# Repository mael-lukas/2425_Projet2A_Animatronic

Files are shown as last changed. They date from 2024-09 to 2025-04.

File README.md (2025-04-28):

<h1 align="center"> DEA : Dynamic Eagle Animatronic</h1>

<p align="center">An english version of this README file can be found below the french one</p>

<h2 align="center">Préambule</h2>
Depuis la Grêce antique et le mythe du géant de bronze Talos, les hommes ont toujours cherchés à créer des automates avec les moyens à leur disposition. Les animatroniques sont l'achèvement actuel de ce désir. Ce sont des poupées mécaniques plus ou moins réalistes dont le fonctionnement interne fait intervenir autant la mécanique que l'électronique.
Elles sont, depuis plusieurs décennies, et encore aujourd'hui principalement utilisées dans le domaine du divertissement au travers des parcs d'attractions, des films et des séries.

Dans le cadre d'un projet de deuxième année à l'école d'ingénieur française ENSEA ( École Nationale Supérieure de l'Électronique et de ses Applications), nous allons continuer la création d'une animatronique d'aigle royal démarrée au second semestre de l'année dernière.

# Sommaire 
  * #### Équipe et détail des tâches
  * #### Électronique et CAO
  * #### Modélisation & Impression 3D
  * #### Mécanique
  * #### Informatique
  * #### Résultat final
  * #### Points d'amélioration
  * #### Conclusion

<table>
  <tr>
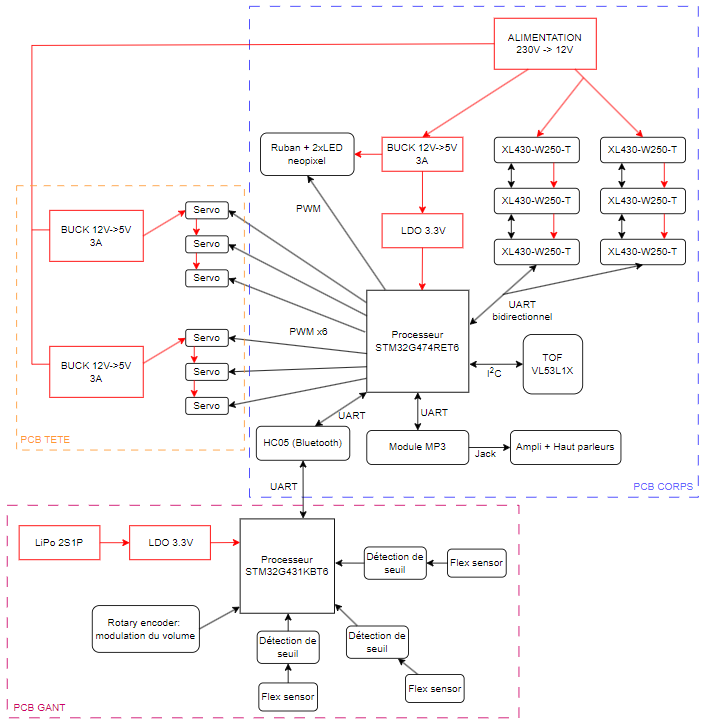
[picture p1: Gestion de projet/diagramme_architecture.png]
Diagramme d'architecture
    <td></td>
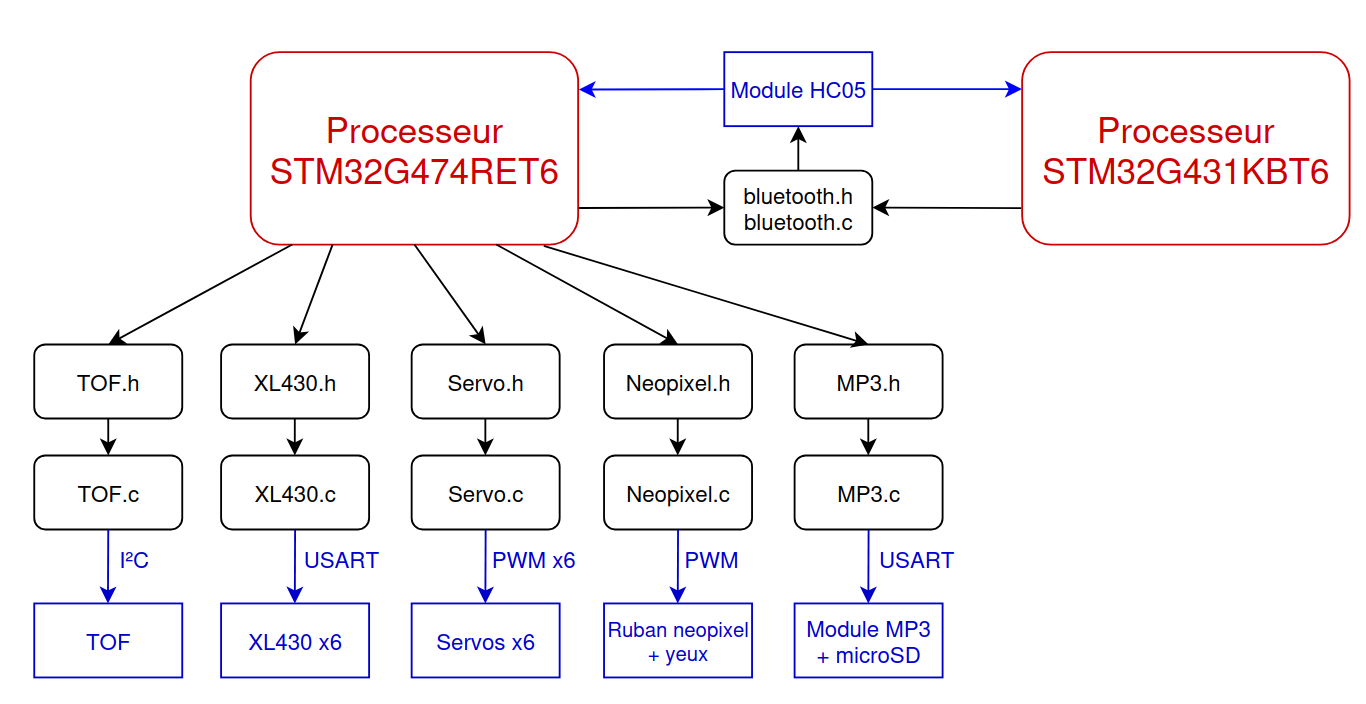
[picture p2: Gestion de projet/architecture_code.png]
Diagramme d'architecture du code
    <td></td>
  </tr>
</table>

<h1 align="center">Équipe</h1>

Membres de l'équipe : 
* #### Vincent Fernandes
    * [Github](https://github.com/FernandesVincent)
    * [Linkedin](https://www.linkedin.com/in/vincent-fernandes-0981552a6/)
* #### Maël Lukas
    * [Github](https://github.com/mael-lukas)
    * [Linkedin](https://www.linkedin.com/in/mael-lukas/)
* ##### Romane Ponthieu
    * [Github](https://github.com/Romanepnth)
    * [Linkedin](https://www.linkedin.com/in/romane-ponthieu/)
* #### Sedrenn Labrousse
    * [Github](https://github.com/Sedrennl)
    * [Linkedin](https://www.linkedin.com/in/sédrenn-labrousse-24b2a5295/)

* #### Supervisé par Nicolas Papazoglou
    * [Github](https://github.com/DBXYD?tab=overview&from=2024-05-01&to=2024-05-29)
    * [Linkedin](https://www.linkedin.com/in/nicolas-papazoglou-38382646/?originalSubdomain=fr)
 
* #### Supervisé par Laurent Fiack
    * [Github](https://github.com/lfiack)
    * [Linkedin](https://fr.linkedin.com/in/laurent-fiack-1b1415124)

Nous vous invitons à consulter notre [github de l'année dernière](https://github.com/mael-lukas/2324_Projet1AB_Animatronic), dans lequel vous pourrez trouver toutes les bases sur lesquelles nous avons démarré ce projet.

Ce projet s'articule autour de plusieurs compétences techniques : informatique, électronique & CAO, modélisation & impression 3D et mécanique. Chacune ayant partagée entre différents membres de l'équipe.

   * Informatique

Cette partie a été majoritairement traitée par Maël avec également, de manière plus minoritaire, Vincent.
Dans cette partie nous allons voir comment tout le code nécessaire au bon fonctionnement du DEA se présente. En partant de simple envoies de PWM pour commander des servomoteurs à la programmation de moteurs plus complexes, en passant par l'allumage de LED neopxiel et de la communication Bluetooth.

   * Électronique & CAO

Cette partie concerne différentes sous compétences : la conception des PCB, la soudure de ceux-ci, les test associés et finalement le sertissage et cablâge. 
Comme notre projet inclus plusieurs PCBs, leur conception a été réalisée par Vincent (pour les PCBs du corps et du gant) et Romane (pour le PCB de la tête).
Les soudures CMS ont été réalisées par Maël et Romane, tandis que les soudures THT ont été effectuées par Vincent.
Le sertissage et le cablâge ont également été réalisé par Vincent.

   * Modélisation & Impression 3D

Cette partie a été essentiellement traitée par Sedrenn aidée de Romane et Vincent. L'objectif de celle-ci étant de modéliser et d'imprimer l'aigle en taille 1:1 ainsi que des caches pour protéger l'alimentation et les PCBs.

   * Mécanique

Cette partie concerne la gestion des différents moteurs qui a été faite par Maël pour l'implémentation du code, par Vincent pour le cablâge de ceux-ci et leur placement sur la structure de l'aigle mais également par Sedrenn et Romane pour la conception des pièces 3D permettant de faire les liaisons entre ceux-ci.

<h1 align="center">Électronique & CAO</h1>

Pour commencer, veuillez trouver ci-dessous le diagramme d'architecture qui nous a servis de base pour la création des PCB de ce projet:

<div align="center">
  Diagramme d'architecture
</div>

Voici donc, le schematic et le routage du PCB principal de projet, le PCB du corps :

<table>
  <tr>
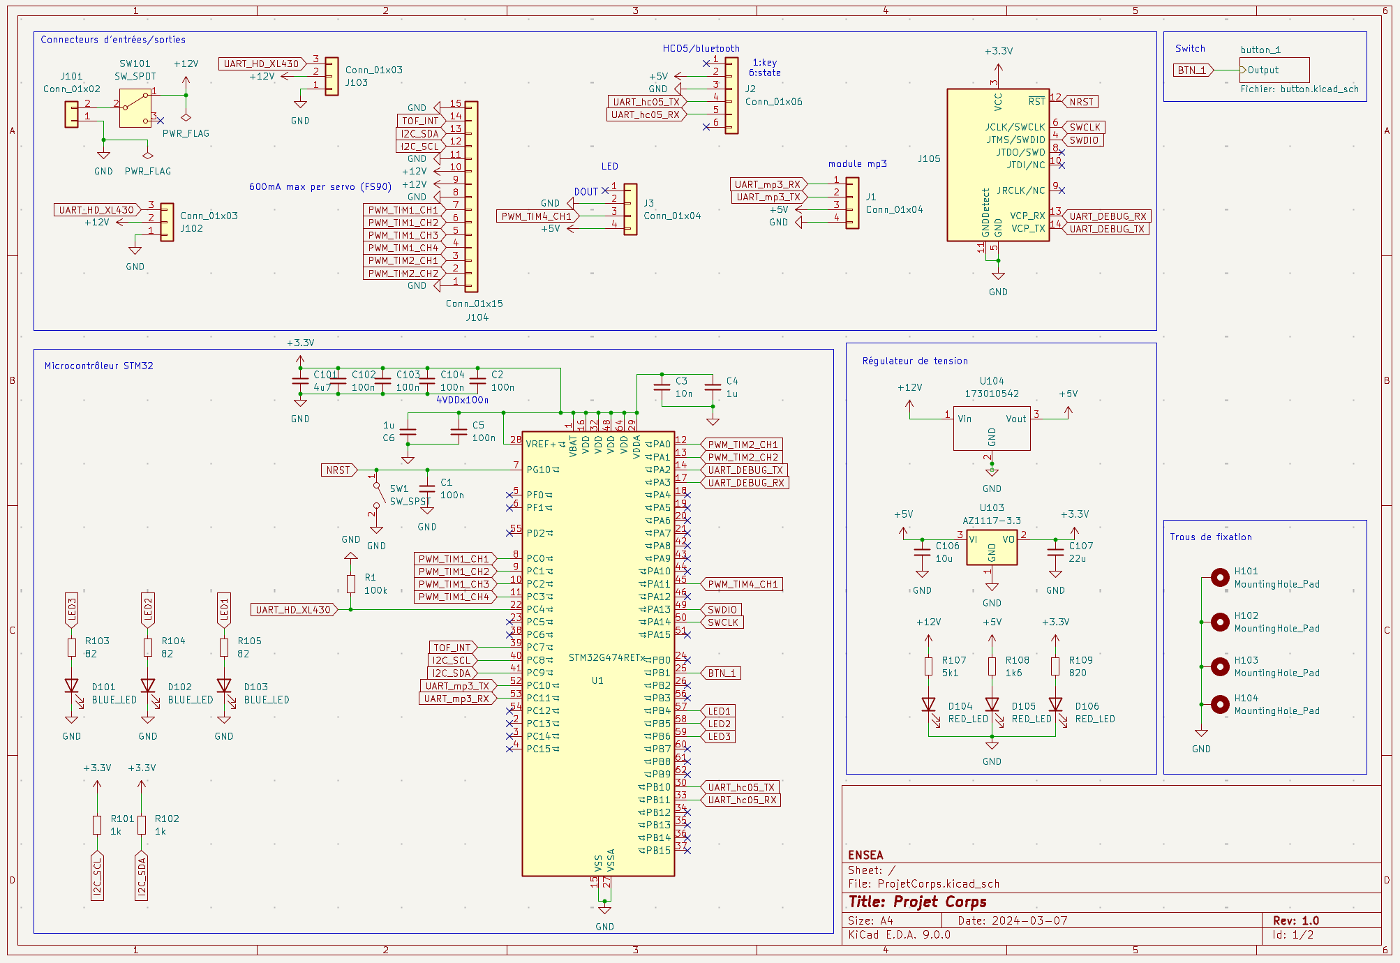
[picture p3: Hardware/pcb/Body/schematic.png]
Schematic
    <td></td>
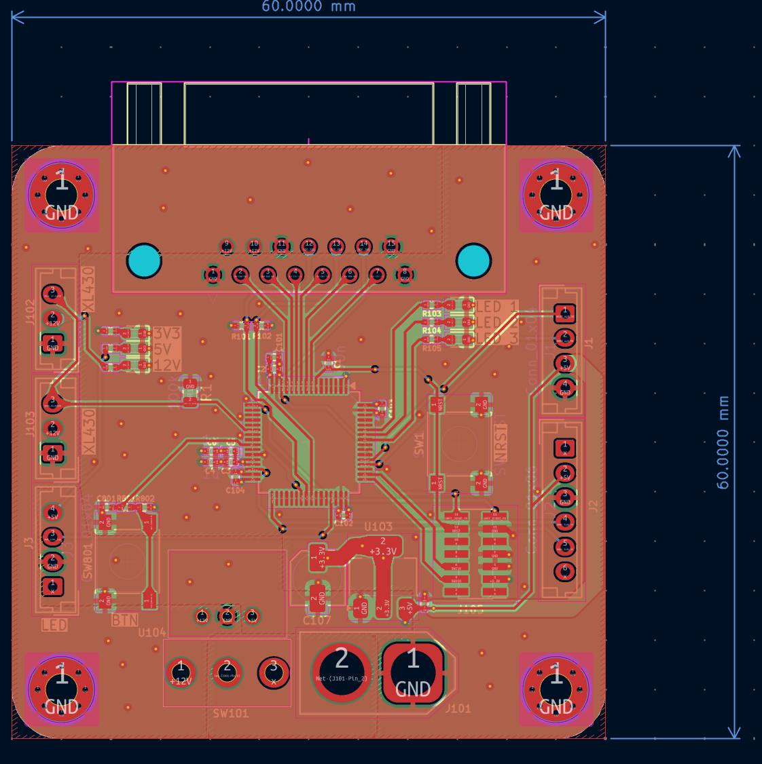
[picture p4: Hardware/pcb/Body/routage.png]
Routage
    <td></td>
  </tr>
</table>

Ce PCB a eu le droit à plusieurs versions afin de l'améliorer à chaque ittération. La dernière en date est l'ajout de R1, une résistance de pull-up pour le protocol UART qui nous sert à commander les moteurs. Cependant, une fois ce nouveau PCB soudé et testé nous n'arrivions plus à communiquer avec les moteurs donc nous sommes repassé sur la version antérieure du PCB, qui elle est foncitonnel, où la résistance de pull-up est activée sur STM32CubeIDE.
Vous pouvez trouvez [ici](https://github.com/mael-lukas/2425_Projet2A_Animatronic/blob/main/Hardware/pcb/Body/ProjetCorps.csv)la BOM de ce PCB.

Le second PCB que nous avons du réalisé est celui de la tête, vous constaterez qu'il n'a pas changé depuis [l'année dernière](https://github.com/mael-lukas/2324_Projet1AB_Animatronic) voici donc simplement son schematic, son routage et sa BOM :

<table>
  <tr>
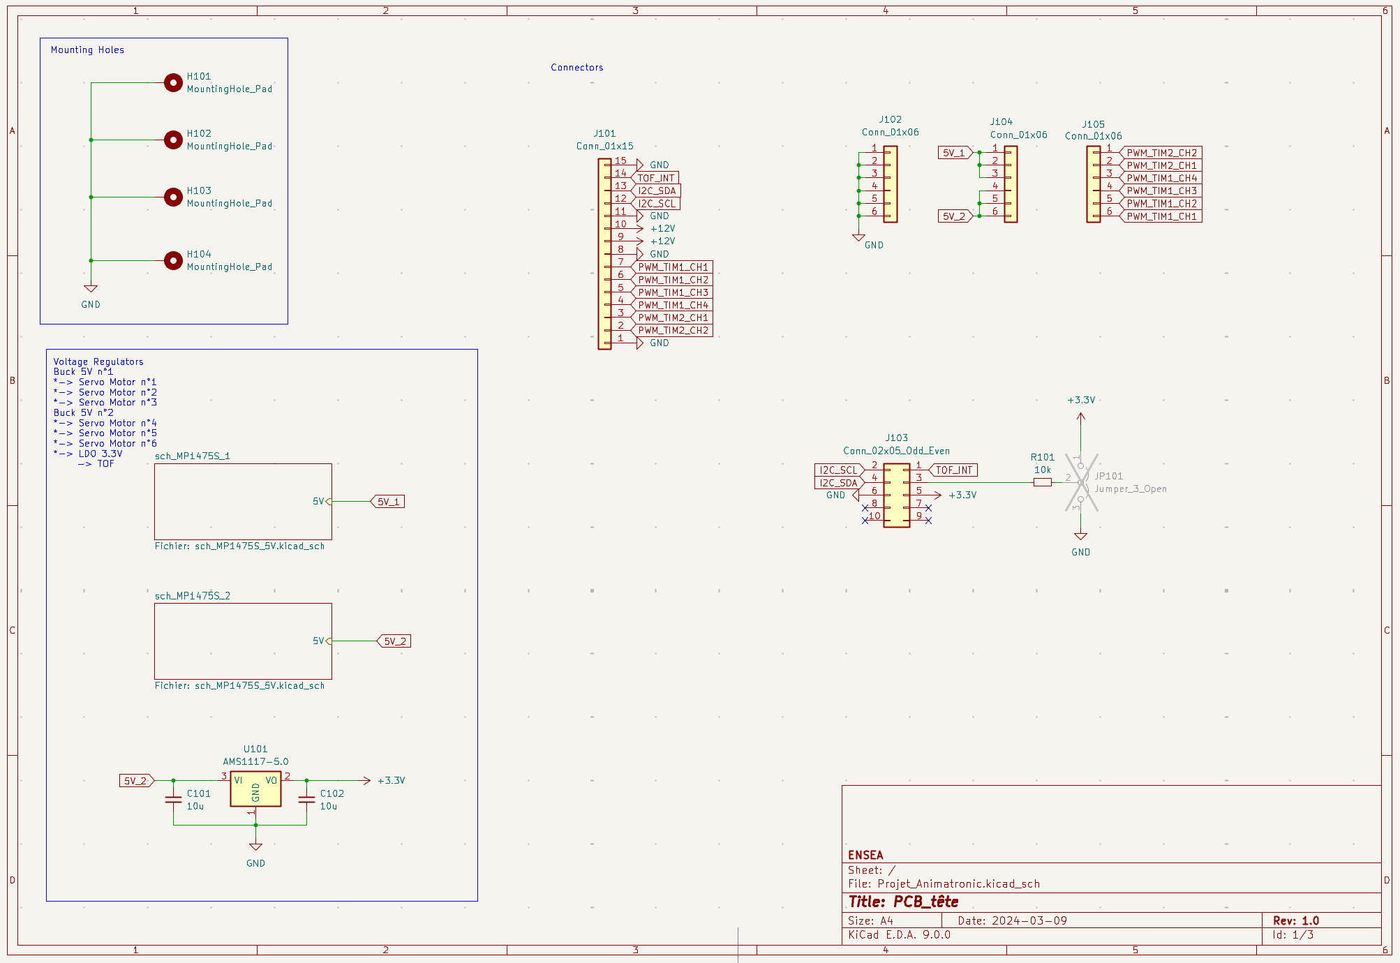
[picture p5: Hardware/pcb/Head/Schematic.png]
Schematic
    <td></td>
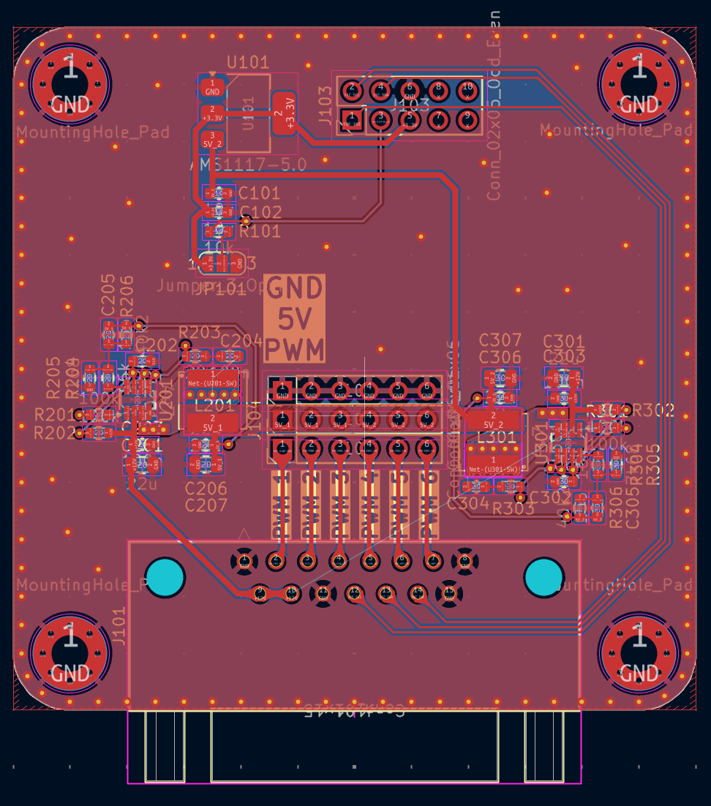
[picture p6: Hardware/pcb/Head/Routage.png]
Routage
    <td></td>
  </tr>
</table>

[BOM](https://github.com/mael-lukas/2425_Projet2A_Animatronic/blob/main/Hardware/pcb/Head/bom%20t%C3%AAte)

Il est à noter qu'avec plus de temps nous aurions suremenent modifier ce PCB car les besoins de notre projet ont changés, nous n'avons plus besoin de contrôler six servomoteurs mais par contre nous avons besoin d'une piste GPIO pour contrôler l'état haut ou bas de la pin XSDN du [TOF](https://github.com/mael-lukas/2425_Projet2A_Animatronic/blob/main/Datasheets/vl53l1x-satel.pdf).

Le troisième et dernier PCB de projet est le PCB du gant qui se présente comme suit :

<table>
  <tr>
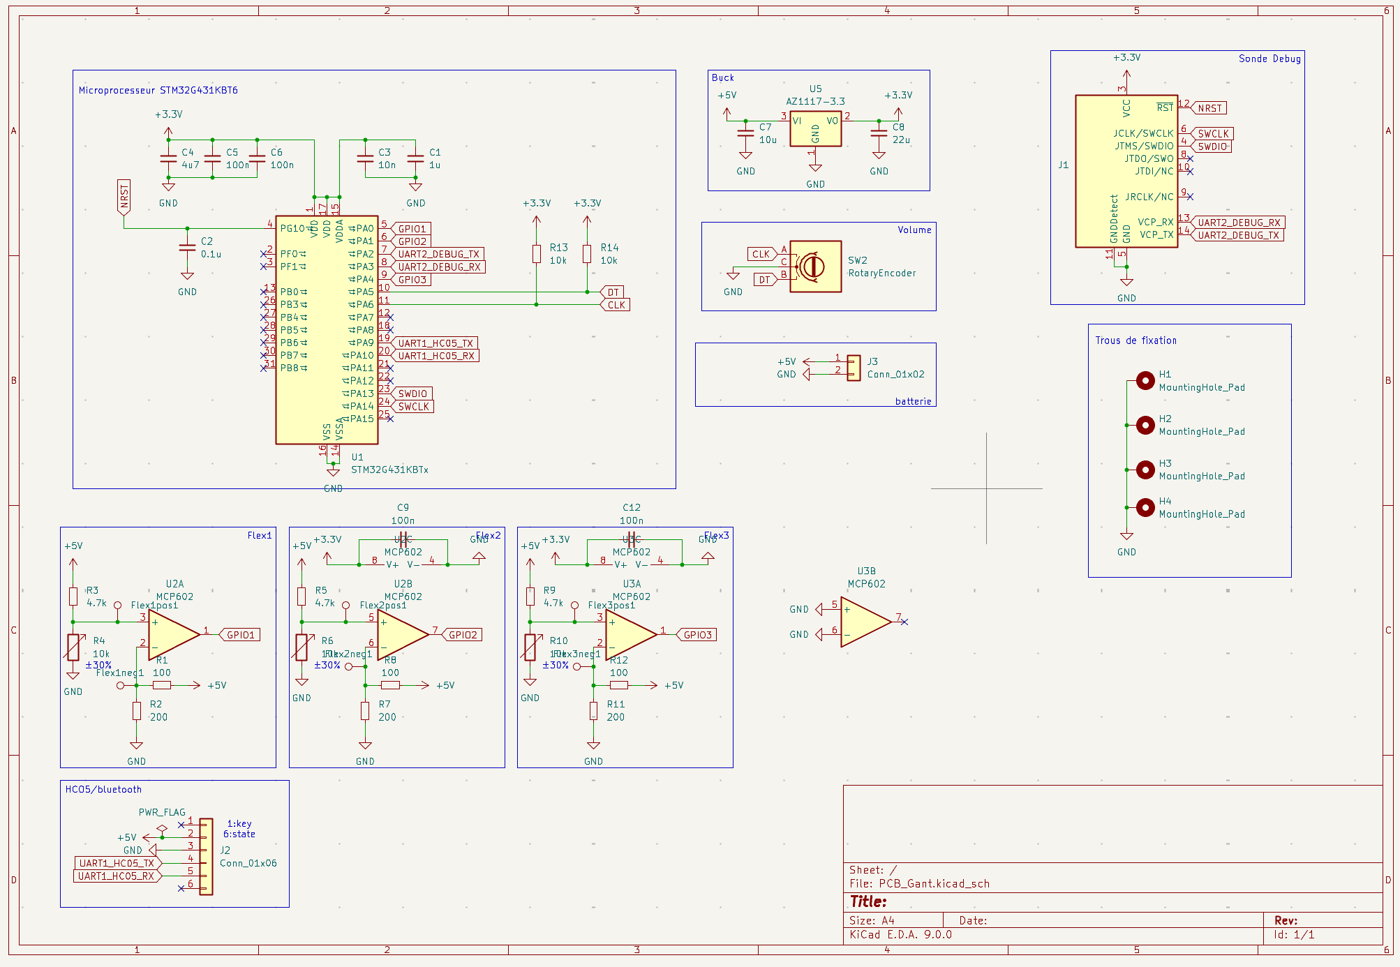
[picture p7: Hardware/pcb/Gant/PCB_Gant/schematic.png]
Schematic
    <td></td>
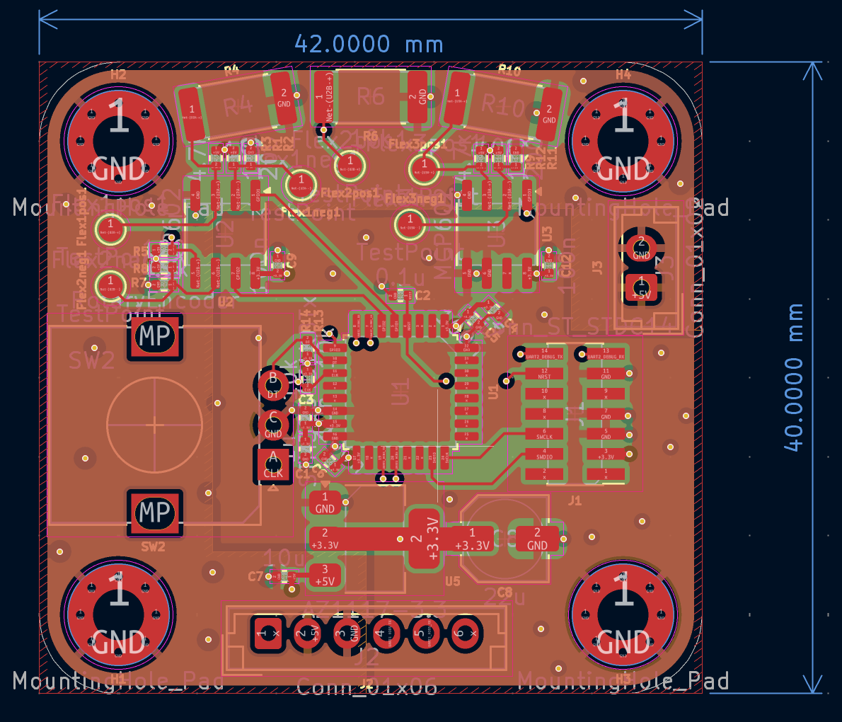
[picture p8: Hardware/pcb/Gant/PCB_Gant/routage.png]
Routage
    <td></td>
  </tr>
</table>

[BOM](https://github.com/mael-lukas/2425_Projet2A_Animatronic/blob/main/Hardware/pcb/Gant/PCB_Gant/PCB_Gant.csv)

L'objectif avec ce PCB est de pouvoir commander les mouvements de l'aigle avec les mouvements de nos doigts et ce sans liaison filaire mais avec une liaison bluetooth grâce au module [HC05](https://github.com/mael-lukas/2425_Projet2A_Animatronic/blob/main/Datasheets/HC-05%20Datasheet.pdf). Les empreintes de résistances en 1206 correspondent aux pads des [flex sensors](https://github.com/mael-lukas/2425_Projet2A_Animatronic/blob/main/Datasheets/Flex_Sensor_Datasheet_v2019a-3304101.pdf) qui sont des résistances variables qui nous permmettent grâce aux circuits visibles sur le schematic d'avoir une tension seuil à partir de laquelle on peut activer tel ou tel mouvement de l'aigle.
Pour pouvoir fonctionner via une liaison Bluetooth nous alimentons le PCB grâce à une batterie Li-ion 1S et grâce à un module servant de Boost pour pouvoir amener une tension de +5V au pcb.

Ce PCB pourrait avoir des versions plus évoluées notamment vis à vis des circuits des [flex sensors](https://github.com/mael-lukas/2425_Projet2A_Animatronic/blob/main/Datasheets/Flex_Sensor_Datasheet_v2019a-3304101.pdf) qui peuvent être largement améliorer afin de par exemple pouvoir changer la tension seuil désirée avec des potentiomètres à la place des résistances.

Ce PCB permet également le contrôle du volume du haut parleur grâce à l'encodeur rotatif présent dessus. Pour revenir rapidement sur cette partie "haut parleur", l'objectif est de pouvoir jouer des sons grâce à un haut parleur présents entre les pattes de l'aigle en fonction de la distance avec la personne en face de lui grâce au [TOF](https://github.com/mael-lukas/2425_Projet2A_Animatronic/blob/main/Datasheets/vl53l1x-satel.pdf).Par exemple, si je me trouve à un mètre de l'oiseau il me dira "Bonjour" par contre si je m'approche à dix centimètres de celui-ci il me dira "Recule".

Pour finir cette partie, vous pouvez voir ci-dessous quelques photos des PCB réaliés. Vous constaterez qu'ils sont chacun entourés d'un support fait en impression 3D. Ces supports ne sont pas nécessaire in fine mais ils permettent d'éviter les risques en empéchant les collisions malheureuses entre les PCB, ce qui pourrait amener des problèmes si cela se passe lorsqu'ils sont en fonctionnement.

<h1 align="center">Modélisation & Impression 3D</h1>

Maintenant que nous avons commencé à parler de modélisation 3D il est temps d'attaquer totalement cette partie. En effet, nous avons décidés d'imprimer l'aigle entièrement en 3D en le vidant bien sûr à l'intérieur afin de pouvoir y placer notre matériel. Nous avons séparés cette modélisation en 3 parties : la tête, les ailes et le reste.

## Tête
C'est sans aucun doute la partie la plus compliquée de cette modélisation car il faut la travailler pour faire en sorte que le bec et les paupières de l'aigle soit amovibles et contrôlables par des servomoteurs. Voici, ci-dessous le modèle 3D et l'impression de celle-ci.

<div align="center">
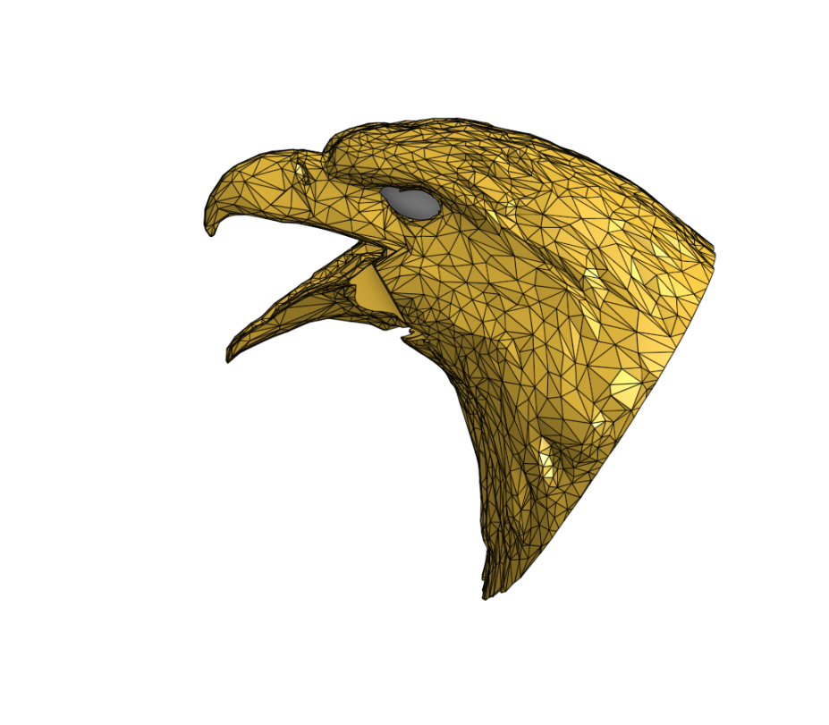
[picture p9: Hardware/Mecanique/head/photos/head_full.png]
modélisation tête
  
</div>

Le modèle 3D a été repris d'un modèle existant, puis il a du être modifié afin notamment de vider l'intérieur, pour permettre le placement des moteurs, mais aussi de rendre la bouche et les paupières ammovibles.

<table>
  <tr>
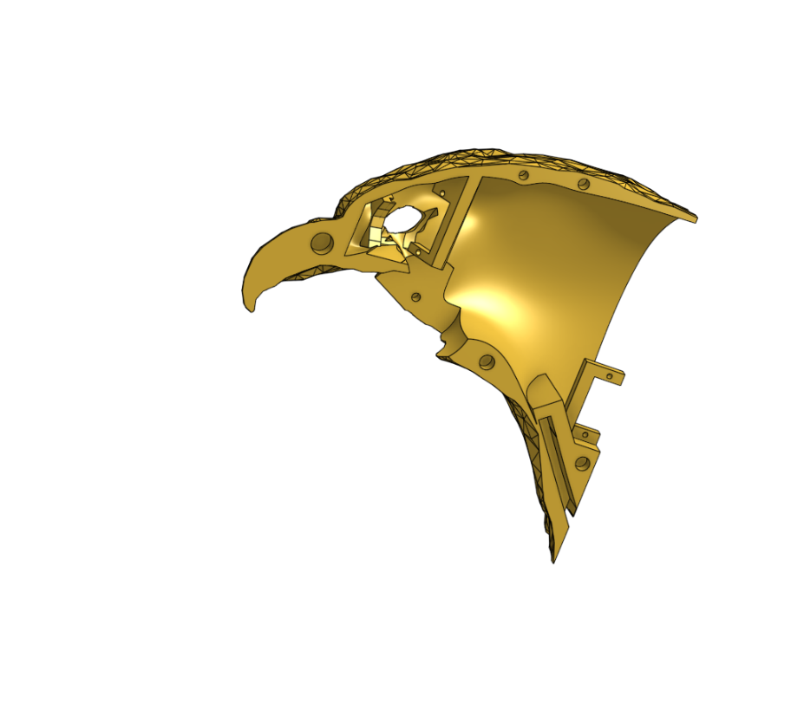
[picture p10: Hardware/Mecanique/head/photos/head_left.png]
tête gauche
    <td></td>
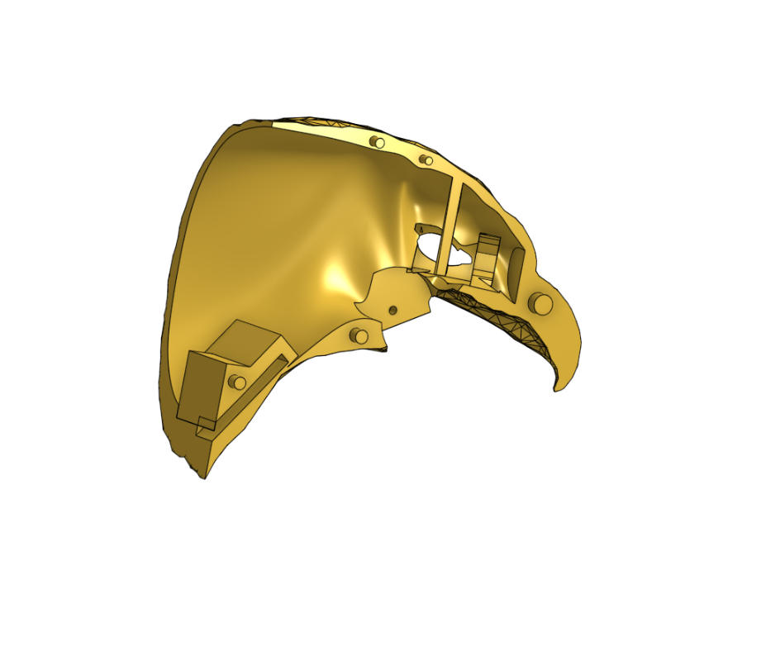
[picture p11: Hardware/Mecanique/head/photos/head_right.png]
tête droite
    <td></td>
  </tr>
</table>

<table>
  <tr>
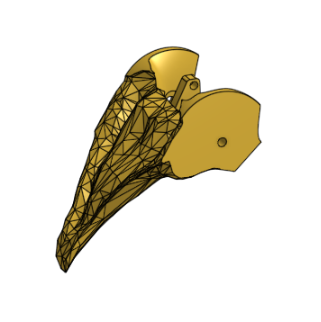
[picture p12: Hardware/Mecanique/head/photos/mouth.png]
bouche
    <td></td>
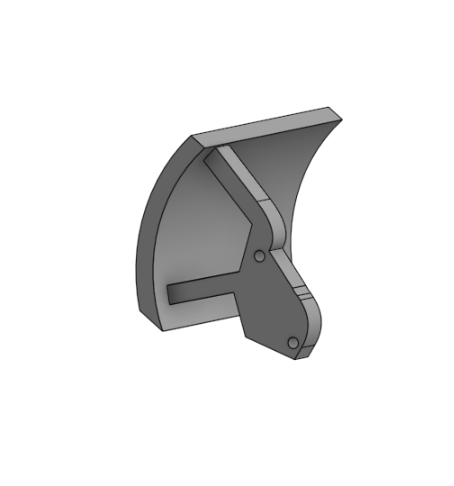
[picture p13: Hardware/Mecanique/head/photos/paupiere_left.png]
paupière gauche
    <td></td>
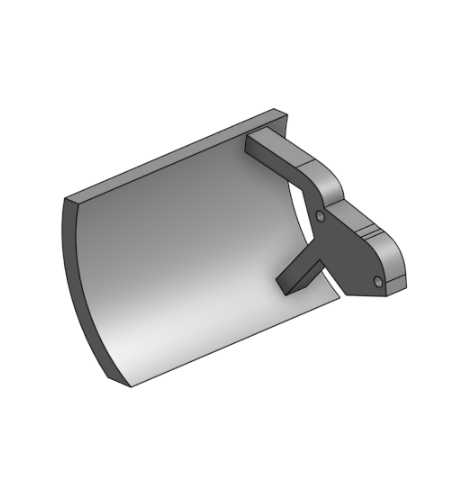
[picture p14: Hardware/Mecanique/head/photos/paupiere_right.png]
paupière droite
    <td></td>
  </tr>
</table>

## Ailes
À l'opposé de la tête, c'est la modééisation la plus simple de projet car elle consiste seulement en la réalisation de pièces permettant d'approximer les os de l'aigle avec des emplacements pour les moteurs de l'épaule et du coude. À cela il faut ajouter les modules rouges que vous pourrez voir ci-après qui permettent la pose des plumes.

<table>
  <tr>
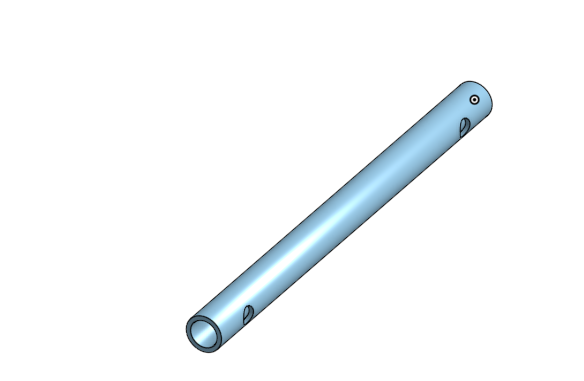
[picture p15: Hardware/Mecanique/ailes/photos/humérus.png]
humerus
    <td></td>
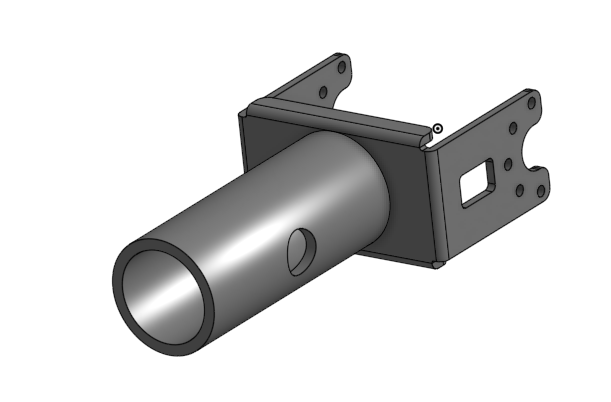
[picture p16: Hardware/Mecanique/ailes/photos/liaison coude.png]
coude
    <td></td>
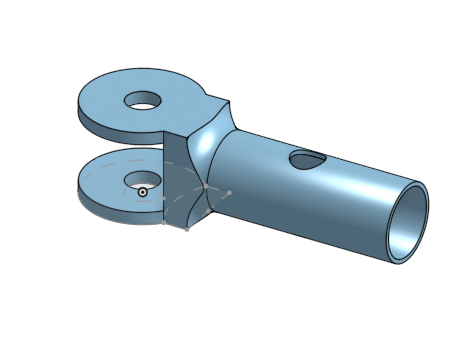
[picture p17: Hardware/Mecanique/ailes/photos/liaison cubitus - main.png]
cubitus
    <td></td>
  </tr>
</table>

<table>
 <tr>
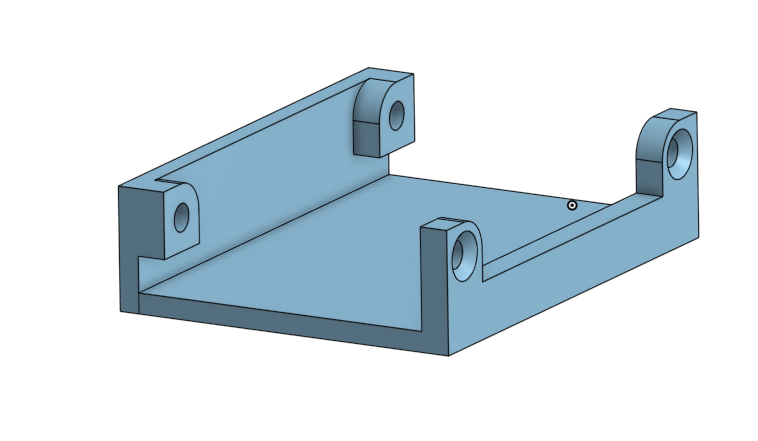
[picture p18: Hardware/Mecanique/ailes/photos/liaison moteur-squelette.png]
moteur squelette
    <td></td>
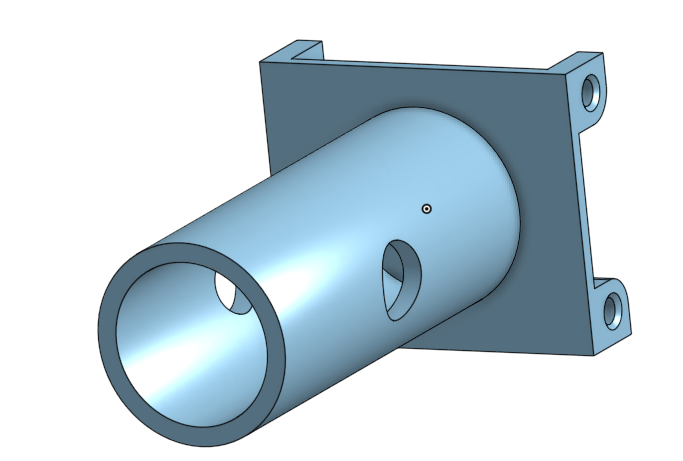
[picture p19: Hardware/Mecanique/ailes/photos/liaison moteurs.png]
moteurs
    <td></td>
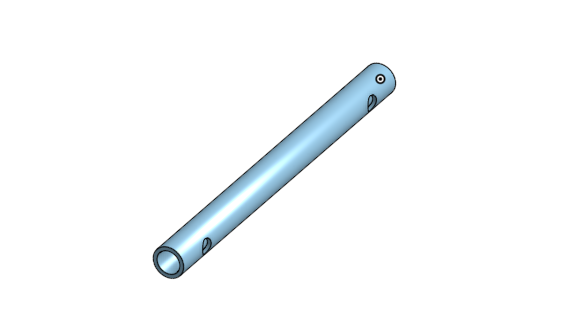
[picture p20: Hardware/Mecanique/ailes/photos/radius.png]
radius
    <td></td>
 </tr>
</table>

## Corps
Au vu du temps disponible, nous avons juste eu le temps de travailler la cage toracique de l'oiseau et donc nous avons délaissé la queue et les pattes qui n'ont pas d'autres utilités à part apporter de l'esthétique au projet, là où l'abdomen possède, lui, un réel intérêt. En effet, il nous permet de ranger à l'intérieur l'ensemble de notre électronique et de notre câblage afin que le projet ne laisse, dans l'idéal, rien apparaître de l'extérieur si tenté un câble d'alimentation.

<table>
  <tr>
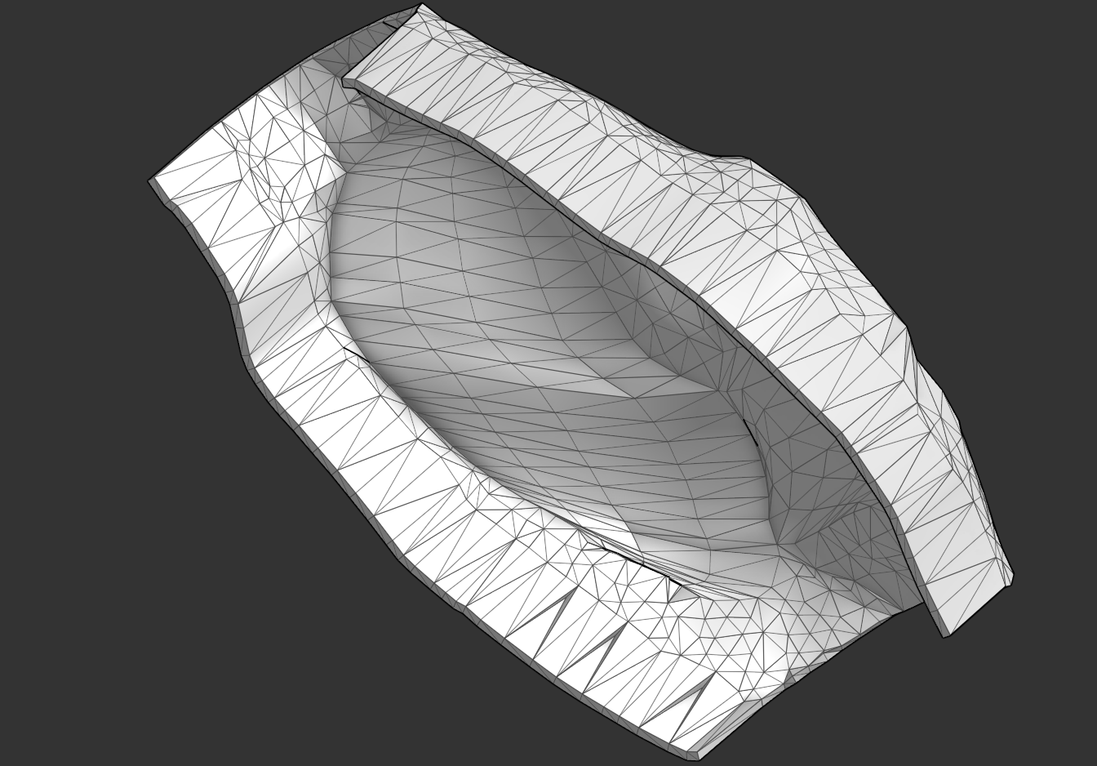
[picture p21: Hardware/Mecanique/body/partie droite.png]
droite
    <td></td>
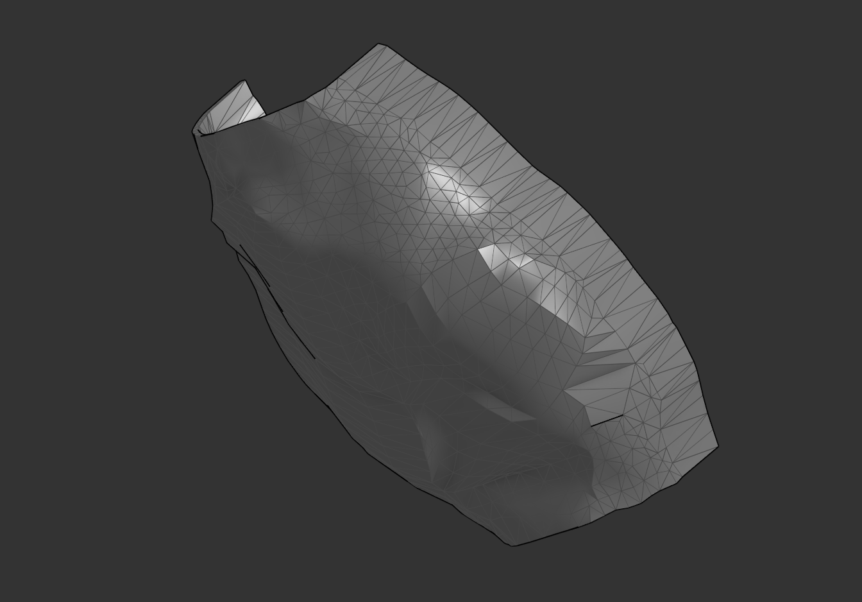
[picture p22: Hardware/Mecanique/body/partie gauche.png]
gauche
    <td></td>
  </tr>
</table>

L'impression du corps à due se faire en quatres parties car nous avions une coontrainte de temps : les impressiosns ne peuvent pas durer plus de 12h et les dimensions des imprimantes 3D qui sont trop petites pour notre modélisation. En effet, les plus grandes imprimantes 3D que nous pssédons sont des Creality K1 Max qui permettent de réaliser des impressions en 300x300x300 or le corps de l'oiseau tend plutôt sur du 350x400x200. De plus, pour l'assemblage de ces quatres parties, au vu du temps mis à disposition pour ce projet nous n'avons pas pu prévoir de moyen d'emboîter et de désemboiter cette partie. Pour que le tout se tienne nous avons donc pris le partit de coller les différentes parties avec un pistolet à colle.

<h1 align="center">Mécanique</h1>

Nous avons rapidement abordé la question des moteurs dans la partie précédente mais pour l'aborder un peu plus en profondeur, nous utilisons deux références de moteurs pour ce projet, les [FS90](https://github.com/mael-lukas/2425_Projet2A_Animatronic/blob/main/Datasheets/FS90.pdf) et les [XL430](https://github.com/mael-lukas/2425_Projet2A_Animatronic/blob/main/Datasheets/XL430-W250-T.pdf). Les premiers sont des servomteur 180° permettant le choix d'une position sur un plage de 180° par l'envoi d'une PWM. Nous les utilisons pour commander le bec et les yeux de l'aigle car cela ne requiert que par de force. De l'autre côté, les XL430 nous servent pour les mouvement plus complexes et surtout qui demandent plus de force. En effet, nous utilisons six de ces moteurs pour réaliser les ailes de l'oiseau, sur chaque aile nous avons deux XL430 qui sont utilisés pour reproduire l'épaule et le troisième pour reproduire ce que nous pourrions appeler le coude. 

Vous l'avez peut-être remarquez sur les photos ci-dessus mais toutes les pièces liants les XL430 ont été réalisées en impression 3D à l'exceptio de la pièce liant les deux moteurs de l'épaule. En effet, nous avions également fait une première version de cette pièce en impression 3D mais le problème était qu'elle doit pouvoir soutenir tout le poids de l'aile. Cela a causé la destruction de la version 3D de la pièce lorsqu'i fallut tester les mouvements de l'aile. Pour pallier à cela nous avons commander la pièce en métal aurpès du fournisseur et c'est donc cette pièce que vous pouvez voir sur les photos ci-dessous:

<table>
  <tr>
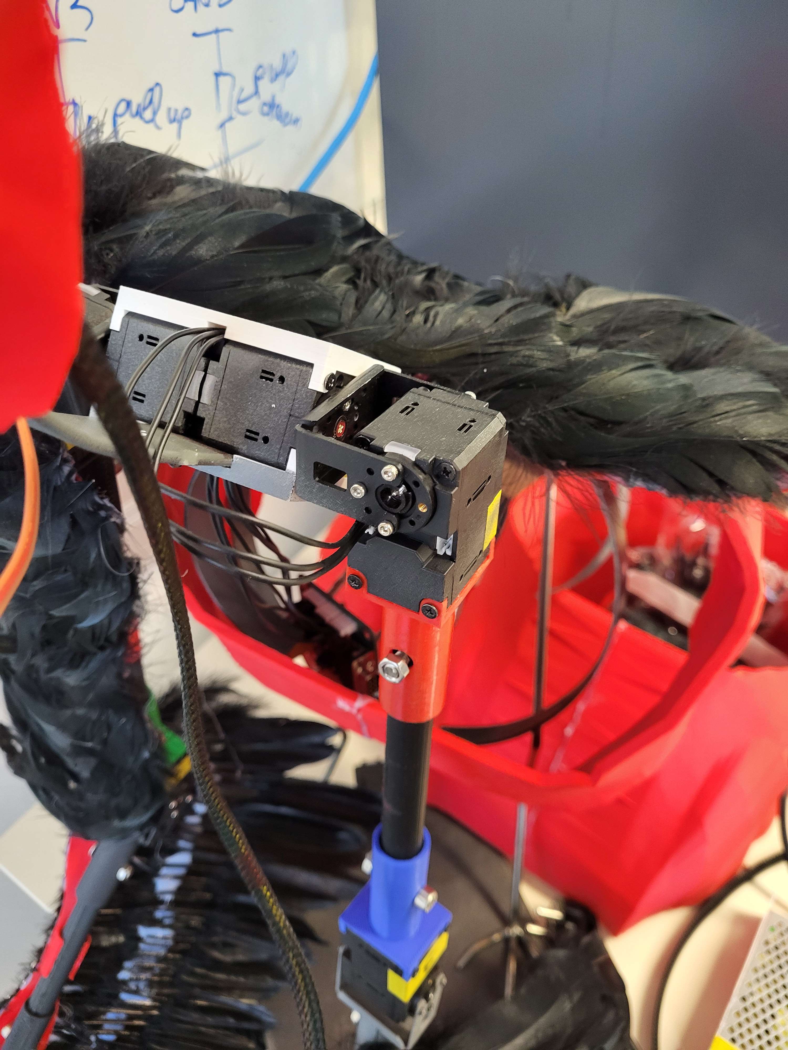
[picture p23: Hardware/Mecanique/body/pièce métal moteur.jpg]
pièce métal droite
    <td></td>
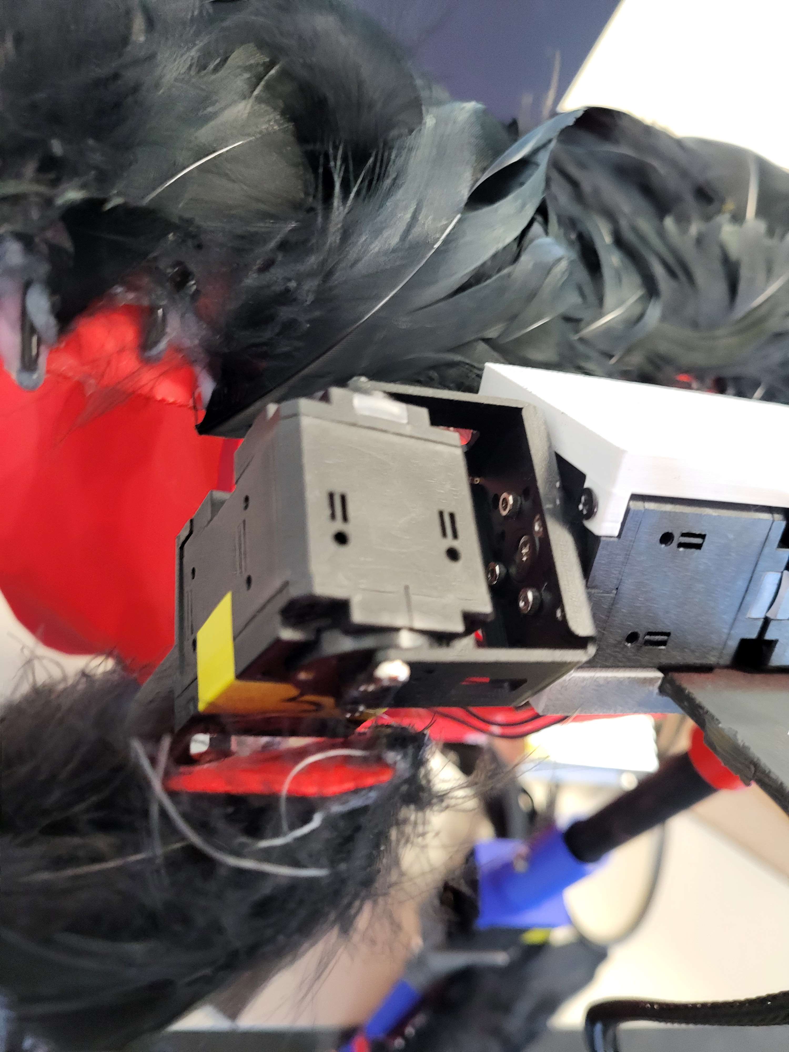
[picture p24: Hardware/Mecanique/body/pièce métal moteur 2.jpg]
pièce métal gauche
    <td></td>
  </tr>
</table>

<h1 align="center">Informatique</h1>

Cependant, tout cela ne pourrait pas fonctionner sans code. Voici, ci-dessous le diagramme d'architecture du code:

<div align="center">
  architecture code
</div>

Nous allons traiter chaque partie de code de gauche à droite d'après ce diagramme en commençant tout d'abord par le code pour la communication bluetooth entre le STM32G474RET6 et le STM32G431KBT6.

Il faut cependant noter que nous n'avons cependant pas eu le temps de le tester correctement.

Pour le code du TOF, cette partie a été particulièrement compliquée pour nous et avions finis par la laisser un peu de côté au profit d'autres parties mais finalement nous avons pu avoir accès à une librairie écrite par M. Fiack et disponible sur son github. En adaptant cette librairie au processeur que nous utilisons nous avons pu faire fonctionner le TOF correctement. 

Les XL4430 sont sans aucun doute la partie la plus complexe de tout le projet, même au bout de tant de temps à travailler dessus nous avons toujours des problèmes dont nous ne comprenons pas la présence. En particulier, lorsque l'exact même code fonctionnait une semaine auparavant.

Les LED neopixel sont quant à elles une partie assez simple que nous avions réussi à faire fonctionner par l'envoi de PWM avant de passer à une version plus avancée grâce à une librairie de M. Fiack qui utilise le DMA.

Finalement, le code du module est surement la partie qui nous a été le plus simple à réalisée et qui nous permet, avec le module suivant : https://www.gotronic.fr/art-module-mp3-uart-mp3player-38215.htm de pouvoir jouer n'importe quel son présent sur la carte micro SD.

<h1 align="center">Résultat final</h1>

Finalement à la fin de ce projet nous avons pu obtenir les résultats suivant :
* contrôle total des LED via DMA
* Audio fonctionnel (Haut parleur + module mp3)
* Moteurs XL430 et FS90 tous fonctionnels
* Modélisations et impressions finalisées
* PCB fonctionnels
* code fonctionnel

CI-dessous vous pouvez télécharger une vidéo avec l'actionnement des 6 moteurs XL430 ainsi que des photos du rendu final de l'aigle:

[Voir la vidéo](https://github.com/mael-lukas/2425_Projet2A_Animatronic/blob/main/Gestion%20de%20projet/moteurs%20fonctionnels.mp4)

<table>
  <tr>
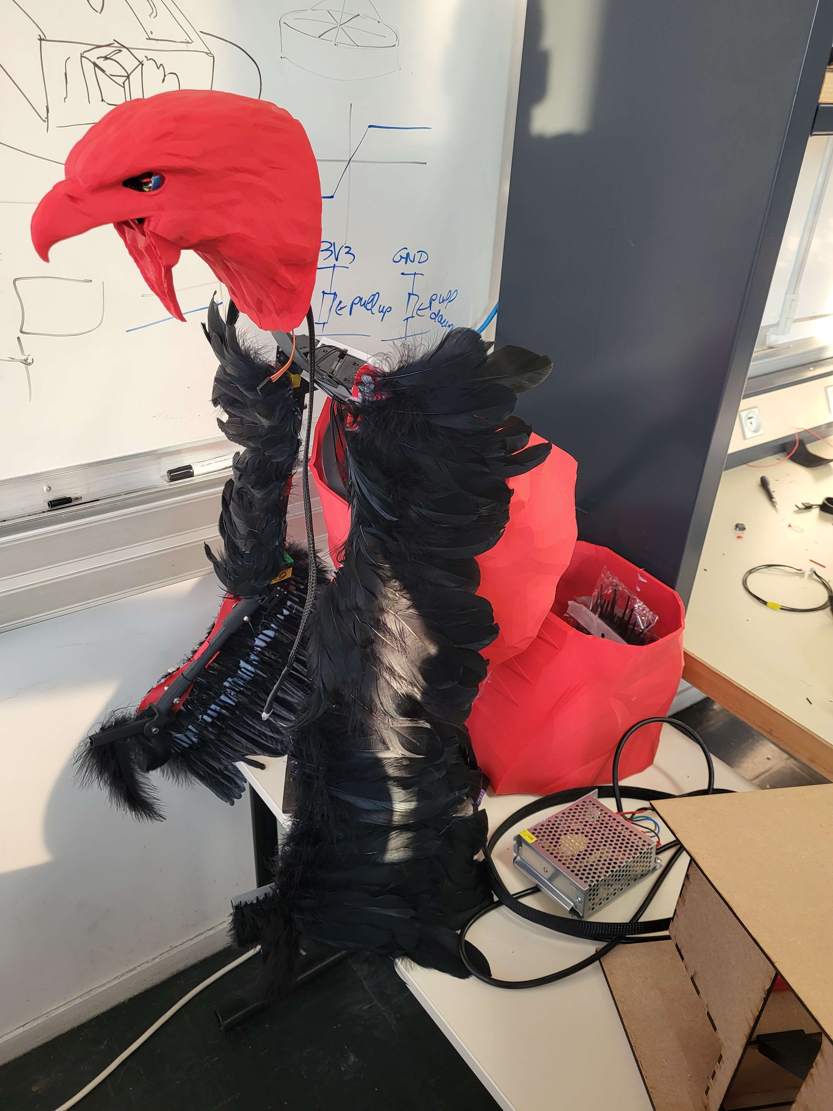
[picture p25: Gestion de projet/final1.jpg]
final 1
    <td></td>
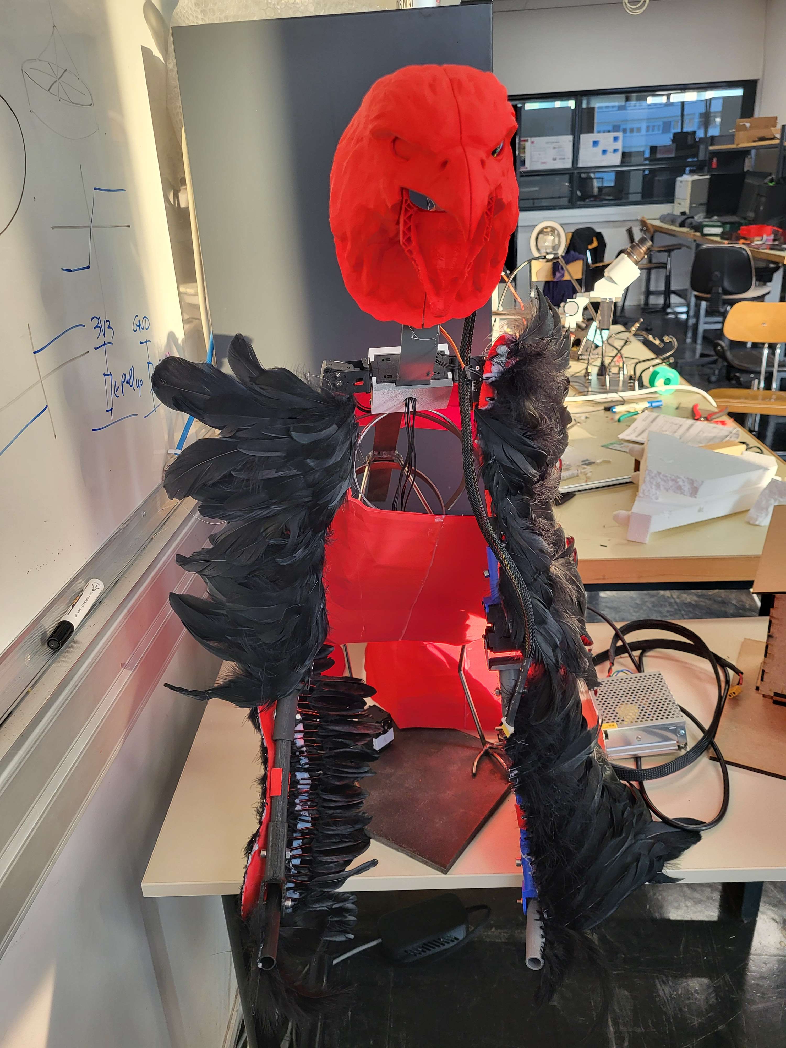
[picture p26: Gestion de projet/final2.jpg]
final 2
    <td></td>
  </tr>
</table>

<h1 align="center">Points d'amélioration</h1>

 Comme vous avez pu le voir le rendu des modélisations 3D n'est vraiment satisfaisant, ce qui devait être un aigle vacille visuellement entre un vautour et un aigle et un dindon.
 Il faudrait donc pour la suite de projet prévoir une refonte totale de l'apparence de l'oiseau quitte à même refaire une base et abandonner l'actuelle en métal.
 De plus, nous n'avons pas réussi à utiliser correctement le capteur de distance, en partie du au fait que le PCB sur lequel il doit être branché date du projet 2324 et qu'il   
 comporte un nombre d'erreurs assez importante. 
 De plus, le PCB du corps mériterait aussi quelques ajustement, notamment au niveau des valeurs et tailles des composants pour qu'ils s'adaptent à ceux que nous avons à l'école.
 Il faudrait également refaire une partie du câblage qui était manquante ou mal faîte à la fin du projet.
 À toutes ces améliorations s'en ajouteront d'autres qui en découlent.
 
<h1 align="center">Conclusion</h1>

Malgré le fait que ce projet n'a pas pu être complété au bout d'un an et demi de travail nous sommes conscient qu'il nous a permis à tous de nous améliorer de façon exponentielle dans chacun des aspects que ce projet à pu couvrir. Nous pensons donc continuer à travailler dessus afin de le finir dans une version bien meilleure version à compter de Septembre durant ce qui sera notre 3ème et dernière annèe à l'ENSEA.

************************************************************************************************************************************************************************************

<h1 align="center">ENGLISH VERSION</h1>

************************************************************************************************************************************************************************************

<h2 align="center">Preamble</h2>
Since ancient Greece and the myth of the bronze giant Talos, humans have always sought to create automatons with the means at their disposal. Animatronics are the current culmination of this desire. They are more or less realistic mechanical dolls whose internal functioning involves both mechanics and electronics.
For several decades, and still today, they are mainly used in the entertainment industry through theme parks, films, and series.

As part of a second-year project at the French engineering school ENSEA (École Nationale Supérieure de l'Électronique et de ses Applications), we will continue the creation of a golden eagle animatronic started in the second semester of last year.

# Table of Contents 
  * #### Team and Task Details
  * #### Electronics and CAD
  * #### 3D Modeling & Printing
  * #### Mechanics
  * #### Computer Science
  * #### Final Result
  * #### Points for Improvement
  * #### Conclusion

<table>
  <tr>
    <td>Architecture Diagram</td>
    <td>Code Architecture Diagram</td>
  </tr>
</table>

<h1 align="center">Team</h1>

Team members: 
* #### Vincent Fernandes
    * [Github](https://github.com/FernandesVincent)
    * [Linkedin](https://www.linkedin.com/in/vincent-fernandes-0981552a6/)
* #### Maël Lukas
    * [Github](https://github.com/mael-lukas)
    * [Linkedin](https://www.linkedin.com/in/mael-lukas/)
* ##### Romane Ponthieu
    * [Github](https://github.com/Romanepnth)
    * [Linkedin](https://www.linkedin.com/in/romane-ponthieu/)
* #### Sedrenn Labrousse
    * [Github](https://github.com/Sedrennl)
    * [Linkedin](https://www.linkedin.com/in/sédrenn-labrousse-24b2a5295/)

* #### Supervised by Nicolas Papazoglou
    * [Github](https://github.com/DBXYD?tab=overview&from=2024-05-01&to=2024-05-29)
    * [Linkedin](https://www.linkedin.com/in/nicolas-papazoglou-38382646/?originalSubdomain=fr)
 
* #### Supervised by Laurent Fiack
    * [Github](https://github.com/lfiack)
    * [Linkedin](https://fr.linkedin.com/in/laurent-fiack-1b1415124)

We invite you to consult our [GitHub from last year](https://github.com/mael-lukas/2324_Projet1AB_Animatronic), where you can find all the foundations on which we based this project.

This project is built around several technical skills: computer science, electronics & CAD, 3D modeling & printing, and mechanics. Each area was divided among different team members.

   * Computer Science

This part was mainly handled by Maël, with some minor contributions from Vincent.
In this section, we will see how all the code necessary for the proper functioning of the DEA is organized. Starting from simple PWM signals to control servomotors, to programming more complex motors, and including the control of neopixel LEDs and Bluetooth communication.

   * Electronics & CAD

This part concerns different sub-skills: PCB design, soldering, associated testing, and finally crimping and cabling.
As our project includes several PCBs, their design was carried out by Vincent (for the body and glove PCBs) and Romane (for the head PCB).
The SMD soldering was done by Maël and Romane, while the THT soldering was carried out by Vincent.
Crimping and cabling were also performed by Vincent.

   * 3D Modeling & Printing

This part was mainly handled by Sedrenn, aided by Romane and Vincent. The goal was to model and print the eagle at a 1:1 scale as well as protective covers for the power supply and PCBs.

   * Mechanics

This part concerns the management of the different motors, which was done by Maël for the code implementation, by Vincent for the wiring of the motors and their placement on the eagle structure, and also by Sedrenn and Romane for the design of the 3D printed parts used to link everything together.

<h1 align="center">Electronics & CAD</h1>

To start, please find below the architecture diagram that served as the basis for the PCB creation for this project:

<div align="center">
  Architecture Diagram
</div>

Here are the schematic and routing of the main project PCB, the body PCB:

<table>
  <tr>
    <td>Schematic</td>
    <td>Routing</td>
  </tr>
</table>

This PCB underwent several versions to improve it with each iteration. The latest version added R1, a pull-up resistor for the UART protocol used to control the motors. However, once this new PCB was soldered and tested, we could no longer communicate with the motors, so we reverted to the previous functional version of the PCB, where the pull-up resistor is activated via STM32CubeIDE.
You can find the [BOM here](https://github.com/mael-lukas/2425_Projet2A_Animatronic/blob/main/Hardware/pcb/Body/ProjetCorps.csv) for this PCB.

The second PCB we had to create is the head PCB, which has not changed since [last year](https://github.com/mael-lukas/2324_Projet1AB_Animatronic). Therefore, here is simply its schematic, routing, and BOM:

<table>
  <tr>
    <td>Schematic</td>
    <td>Routing</td>
  </tr>
</table>

[BOM](https://github.com/mael-lukas/2425_Projet2A_Animatronic/blob/main/Hardware/pcb/Head/bom%20t%C3%AAte)

It should be noted that, with more time, we would probably have modified this PCB because our project needs have changed: we no longer need to control six servomotors, but we do need a GPIO track to control the high or low state of the XSDN pin of the [TOF](https://github.com/mael-lukas/2425_Projet2A_Animatronic/blob/main/Datasheets/vl53l1x-satel.pdf).

The third and final project PCB is the glove PCB, which is presented as follows:

<table>
  <tr>
    <td>Schematic</td>
    <td>Routing</td>
  </tr>
</table>

[BOM](https://github.com/mael-lukas/2425_Projet2A_Animatronic/blob/main/Hardware/pcb/Gant/PCB_Gant/PCB_Gant.csv)

The goal with this PCB is to control the eagle's movements using our finger motions without a wired connection, but through Bluetooth communication via the [HC05](https://github.com/mael-lukas/2425_Projet2A_Animatronic/blob/main/Datasheets/HC-05%20Datasheet.pdf) module. The 1206 resistor footprints correspond to the pads of the [flex sensors](https://github.com/mael-lukas/2425_Projet2A_Animatronic/blob/main/Datasheets/Flex_Sensor_Datasheet_v2019a-3304101.pdf), which are variable resistors. Thanks to the circuits shown in the schematic, we can detect a threshold voltage that triggers specific eagle movements.

To function via Bluetooth, the PCB is powered by a 1S Li-ion battery, and a boost module is used to bring the voltage up to +5V for the PCB.

This PCB could evolve further, especially regarding the circuits for the [flex sensors](https://github.com/mael-lukas/2425_Projet2A_Animatronic/blob/main/Datasheets/Flex_Sensor_Datasheet_v2019a-3304101.pdf), which could be improved significantly, for example, by allowing adjustable threshold voltages using potentiometers instead of fixed resistors.

The PCB also enables control of the speaker volume through the rotary encoder present on it. Speaking of the "speaker" part, the goal here is to play sounds using a speaker located between the eagle's legs, depending on the distance from the person in front of it via the [TOF sensor](https://github.com/mael-lukas/2425_Projet2A_Animatronic/blob/main/Datasheets/vl53l1x-satel.pdf).  
For instance, if I am one meter away, the eagle will say "Hello", whereas if I move to ten centimeters, it will say "Back off."

To conclude this section, you can see below a few photos of the assembled PCBs. You will notice that each one is surrounded by a 3D-printed protective support. These supports are not strictly necessary but help avoid risks by preventing accidental collisions with the PCBs, which could cause malfunctions during operation.

<h1 align="center">3D Modeling & Printing</h1>

Now that we have started talking about 3D modeling, it's time to fully dive into this part. Indeed, we decided to entirely 3D-print the eagle, making it hollow inside to accommodate our hardware.  
We divided the modeling into three parts: the head, the wings, and the body.

## Head
This is undoubtedly the most complex part of the modeling because it must be adapted so that the eagle’s beak and eyelids are movable and controllable via servomotors. Below are the 3D model and the printed version.

<div align="center">
  Head Model
</div>

The 3D model was based on an existing model but was modified, particularly to hollow out the inside to place the motors, and to make the beak and eyelids movable.

<table>
  <tr>
    <td>Head Left</td>
    <td>Head Right</td>
  </tr>
</table>

<table>
  <tr>
    <td>Mouth</td>
    <td>Left Eyelid</td>
    <td>Right Eyelid</td>
  </tr>
</table>

## Wings
Contrary to the head, this was the simplest part to model. It only involved creating parts to approximate the eagle’s bones and include mounts for the shoulder and elbow motors.  
Additionally, there are small red modules that allow the attachment of the feathers.

<table>
  <tr>
    <td>Humerus</td>
    <td>Elbow</td>
    <td>Cubitus</td>
  </tr>
</table>

<table>
 <tr>
    <td>Motor-Skeleton Link</td>
    <td>Motor Links</td>
    <td>Radius</td>
 </tr>
</table>

## Body
Given the limited time, we only managed to model the eagle’s ribcage.  
The tail and legs were omitted as they are mainly aesthetic, whereas the torso has a practical role: it houses all the electronics and wiring to ensure that ideally, no cables are visible externally (except the power cable).

<table>
  <tr>
    <td>Right Part</td>
    <td>Left Part</td>
  </tr>
</table>

The body was printed in four parts due to time constraints (no prints over 12h allowed) and because the available 3D printers were too small.  
Our largest printers, the Creality K1 Max, allow prints up to 300x300x300 mm, but the eagle's body was closer to 350x400x200 mm.  
Additionally, due to time limitations, we could not design interlocking assembly parts, so the four sections were simply glued together using a hot glue gun.

<h1 align="center">Mechanics</h1>

We briefly mentioned the motors earlier, but to go deeper:  
We used two motor types: [FS90](https://github.com/mael-lukas/2425_Projet2A_Animatronic/blob/main/Datasheets/FS90.pdf) and [XL430](https://github.com/mael-lukas/2425_Projet2A_Animatronic/blob/main/Datasheets/XL430-W250-T.pdf).  
The FS90 are small 180° servomotors controlled by PWM signals, used for light-duty tasks such as controlling the beak and eyelids.  
The XL430, on the other hand, are more powerful and were used for heavier movements such as the wings, where strength is necessary.  
Each wing uses three XL430 motors: two for the shoulder and one for the elbow.

You may have noticed in the previous photos that all the parts connecting the XL430s were 3D-printed, except for the part linking the two shoulder motors.  
Initially, this was also 3D-printed, but it broke during testing due to the stress.  
Thus, we ordered a metal replacement from the supplier, as shown below:

<table>
  <tr>
    <td>Metal Motor Part Right</td>
    <td>Metal Motor Part Left</td>
  </tr>
</table>

<h1 align="center">Computer Science</h1>

However, all of this would not work without code. Below is the architecture diagram of the code:

<div align="center">
  architecture code
</div>

We will address each part of the code from left to right according to this diagram, starting first with the code for Bluetooth communication between the STM32G474RET6 and the STM32G431KBT6.

It should be noted, however, that we did not have time to properly test it.

As for the TOF code, this part was particularly complicated for us, and we ended up leaving it aside in favor of other parts, but eventually, we were able to access a library written by Mr. Fiack and available on his GitHub. By adapting this library to the processor we are using, we were able to get the TOF working correctly.

The XL4430 motors are undoubtedly the most complex part of the entire project. Even after so much time working on them, we still encounter issues that we do not understand. In particular, the exact same code worked a week ago.

The neopixel LEDs, on the other hand, are quite simple, and we were able to get them working by sending PWM signals before moving to a more advanced version using a library by Mr. Fiack that utilizes DMA.

Finally, the code for the MP3 module was probably the simplest part for us to develop. With this module: https://www.gotronic.fr/art-module-mp3-uart-mp3player-38215.htm, we were able to play any sound on the micro SD card.

<h1 align="center">Final Result</h1>

At the end of this project, we were able to achieve the following results:
* Full control of the LEDs via DMA
* Functional audio (Speaker + MP3 module)
* Functional XL430 and FS90 motors
* Finalized models and prints
* Functional PCBs
* Functional code

Below you can download a video showing the operation of the 6 XL430 motors, as well as photos of the final rendering of the eagle:

[View the video](https://github.com/mael-lukas/2425_Projet2A_Animatronic/blob/main/Gestion%20de%20projet/moteurs%20fonctionnels.mp4)

<table>
  <tr>
    <td>final 1</td>
    <td>final 2</td>
  </tr>
</table>

<h1 align="center">Points for Improvement</h1>

As you can see, the 3D modeling results are not really satisfactory. What was supposed to be an eagle visually fluctuates between an eagle, a vulture, and a turkey. Therefore, for the continuation of the project, it would be necessary to redesign the appearance of the bird, possibly even remaking the base and abandoning the current metal one. Furthermore, we were not able to use the distance sensor properly, partly due to the fact that the PCB it should be connected to dates from the 2324 project and contains quite a few significant errors. Additionally, the PCB for the body would also require some adjustments, particularly in terms of the values and sizes of components to make them fit those we have at school. The wiring also needs to be redone, as it was missing or poorly done by the end of the project. Many more improvements will come as a result of these.

<h1 align="center">Conclusion</h1>

Although this project could not be completed after a year and a half of work, we are aware that it allowed all of us to improve exponentially in each of the aspects that this project covered. Therefore, we plan to continue working on it to finish it in a much better version starting in September during what will be our 3rd and final year at ENSEA.

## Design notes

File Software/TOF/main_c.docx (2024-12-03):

/* Includes ------------------------------------------------------------------*/

#include "main.h"

/* Private includes ----------------------------------------------------------*/

/* USER CODE BEGIN Includes */

#include "vl53l1_platform.h"

#include "VL53L1X_api.h"

/* USER CODE END Includes */

/* Private typedef -----------------------------------------------------------*/

/* USER CODE BEGIN PTD */

/* USER CODE END PTD */

/* Private define ------------------------------------------------------------*/

/* USER CODE BEGIN PD */

#define VL53L1__ADDR 0x52

#ifdef __GNUC__

#define PUTCHAR_PROTOTYPE int __io_putchar(int ch)

#else

#define PUTCHAR_PROTOTYPE int fputc(int ch, FILE *f)

#endif

/* USER CODE END PD */

/* Private macro -------------------------------------------------------------*/

/* USER CODE BEGIN PM */

/* USER CODE END PM */

/* Private variables ---------------------------------------------------------*/

I2C_HandleTypeDef hi2c3;

UART_HandleTypeDef huart2;

/* USER CODE BEGIN PV */

/* USER CODE END PV */

/* Private function prototypes -----------------------------------------------*/

void SystemClock_Config(void);

static void MX_GPIO_Init(void);

static void MX_I2C3_Init(void);

static void MX_USART2_UART_Init(void);

/* USER CODE BEGIN PFP */

/* USER CODE END PFP */

/* Private user code ---------------------------------------------------------*/

/* USER CODE BEGIN 0 */

PUTCHAR_PROTOTYPE {

HAL_UART_Transmit(&huart2, (uint8_t *)&ch, 1, HAL_MAX_DELAY);

return ch;

}

/* USER CODE END 0 */

/**

* @brief The application entry point.

* @retval int

*/

int main(void)

{

/* USER CODE BEGIN 1 */

/* USER CODE END 1 */

/* MCU Configuration--------------------------------------------------------*/

/* Reset of all peripherals, Initializes the Flash interface and the Systick. */

HAL_Init();

/* USER CODE BEGIN Init */

/* USER CODE END Init */

/* Configure the system clock */

SystemClock_Config();

/* USER CODE BEGIN SysInit */

/* USER CODE END SysInit */

/* Initialize all configured peripherals */

MX_GPIO_Init();

MX_I2C3_Init();

MX_USART2_UART_Init();

/* USER CODE BEGIN 2 */

void I2C_Scan(I2C_HandleTypeDef *hi2c) {

printf("Scanning I2C bus...\r\n");

for (uint8_t addr = 0x01; addr < 0x7F; addr++) {

if (HAL_I2C_IsDeviceReady(hi2c, addr << 1, 1, 10) == HAL_OK) {

printf("Device found at 0x%02X\r\n", addr);

}

}

printf("Scan complete.\r\n");

}

uint8_t initStatus = VL53L1__Init();

if (initStatus != 0) {

printf("Erreur lors de l'initialisation du capteur ! Code erreur: %d\r\n", initStatus);

while (1);

}

printf("Capteur VL53L1X initialisé avec succès.\r\n");

uint16_t distance = 0;

uint8_t status;

/* USER CODE END 2 */

/* Infinite loop */

/* USER CODE BEGIN WHILE */

while (1)

{

// Lecture de la distance

status = VL53L1__GetDistance(&distance);

if (status == 0) {

printf("Distance mesurée: %d mm\r\n", distance);

} else {

printf("Erreur de lecture de la distance. Code erreur: %d\r\n", status);

}

HAL_Delay(500);

/* USER CODE END WHILE */

/* USER CODE BEGIN 3 */

}

/* USER CODE END 3 */

}

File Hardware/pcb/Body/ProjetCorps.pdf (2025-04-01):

### ProjetCorps

Reference | Value | Footprint | Qty | DNP
C1,C2,C5,C102,C103,C104 | 100n | Capacitor_SMD:C_0402_1005Metric | 6
C3,C801 | 10n | Capacitor_SMD:C_0402_1005Metric | 2
C4,C6 | 1u | Capacitor_SMD:C_0402_1005Metric | 2
C101 | 4u7 | Capacitor_SMD:C_0402_1005Metric | 1
C106 | 10u | Capacitor_SMD:C_0402_1005Metric | 1
C107 | 22u | Capacitor_SMD:C_Elec_5x5.4 | 1
D101,D102,D103 | BLUE_LED | LED_SMD:LED_0603_1608Metric | 3
D104,D105,D106 | RED_LED | LED_SMD:LED_0603_1608Metric | 3
H101,H102,H103,H104 | MountingHole_Pad | MountingHole:MountingHole_3.2mm_M3_Pad_Via | 4
J1,J3 | Conn_01x04 | Connector_JST:JST_EH_B4B-EH-A_1x04_P2.50mm_Vertical | 2
J2 | Conn_01x06 | Connector_JST:JST_EH_B6B-EH-A_1x06_P2.50mm_Vertical | 1
J101 | Conn_01x02 | Connector_AMASS:AMASS_XT60-M_1x02_P7.20mm_Vertical | 1
J102,J103 | Conn_01x03 | Connector_JST:JST_EH_B3B-EH-A_1x03_P2.50mm_Vertical | 2
J104 | Conn_01x15 | libs:CONN15_31321_WRE | 1
J105 | Conn_ST_STDC14 | Connector_PinHeader_1.27mm:PinHeader_2x07_P1.27mm_Vertical_SMD | 1
R1 | 100k | Resistor_SMD:R_0805_2012Metric | 1
R101,R102 | 1k | Resistor_SMD:R_0402_1005Metric | 2
R103,R104,R105 | 82 | Resistor_SMD:R_0402_1005Metric | 3
R107 | 5k1 | Resistor_SMD:R_0402_1005Metric | 1
R108 | 1k6 | Resistor_SMD:R_0402_1005Metric | 1
R109 | 820 | Resistor_SMD:R_0402_1005Metric | 1
R801,R802 | 10k | Resistor_SMD:R_0402_1005Metric | 2
SW1,SW801 | SW_SPST | Button_Switch_SMD:SW_Push_1P1T_NO_6x6mm_H9.5mm | 2
SW101 | SW_SPDT | mylib:472123010111 | 1
U1 | STM32G474RETx | Package_QFP:LQFP-64_10x10mm_P0.5mm | 1
U103 | AZ1117-3.3 | Package_TO_SOT_SMD:SOT-223-3_TabPin2 | 1
U104 | 173010542 | Library:173010542 | 1

1

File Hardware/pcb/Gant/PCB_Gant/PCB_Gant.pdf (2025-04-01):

### PCB_Gant

Reference | Value | Footprint | Qty | DNP
C1 | 1u | Capacitor_SMD:C_0402_1005Metric | 1
C2 | 0.1u | Capacitor_SMD:C_0402_1005Metric | 1
C3 | 10n | Capacitor_SMD:C_0402_1005Metric | 1
C4 | 4u7 | Capacitor_SMD:C_0402_1005Metric | 1
C5,C6,C9,C12 | 100n | Capacitor_SMD:C_0402_1005Metric | 4
C7 | 10u | Capacitor_SMD:C_0402_1005Metric | 1
C8 | 22u | Capacitor_SMD:C_Elec_5x5.4 | 1
Flex1neg1,Flex1pos1,Flex2neg1,Flex2pos1,Flex3neg1,Flex3pos1 | TestPoint | TestPoint:TestPoint_Pad_D1.5mm | 6
H1,H2,H3,H4 | MountingHole_Pad | MountingHole:MountingHole_3.2mm_M3_Pad_Via | 4
J1 | Conn_ST_STDC14 | Connector_PinHeader_1.27mm:PinHeader_2x07_P1.27mm_Vertical_SMD | 1
J2 | Conn_01x06 | Connector_JST:JST_EH_B6B-EH-A_1x06_P2.50mm_Vertical | 1
J3 | Conn_01x02 | Connector_JST:JST_EH_B2B-EH-A_1x02_P2.50mm_Vertical | 1
R1,R4,R6,R8,R10,R12,R13,R14 | 10k | -- valeurs mixées -- | 8
R2,R7,R11 | 20k | Resistor_SMD:R_0402_1005Metric | 3
R3,R5,R9 | 4.7k | Resistor_SMD:R_0402_1005Metric | 3
SW2 | RotaryEncoder | Rotary_Encoder:RotaryEncoder_Alps_EC12E_Vertical_H20mm | 1
U1 | STM32G431KBTx | Package_QFP:LQFP-32_7x7mm_P0.8mm | 1
U2,U3 | MCP602 | Package_SO:SOIC-8_3.9x4.9mm_P1.27mm | 2
U5 | AZ1117-3.3 | Package_TO_SOT_SMD:SOT-223-3_TabPin2 | 1

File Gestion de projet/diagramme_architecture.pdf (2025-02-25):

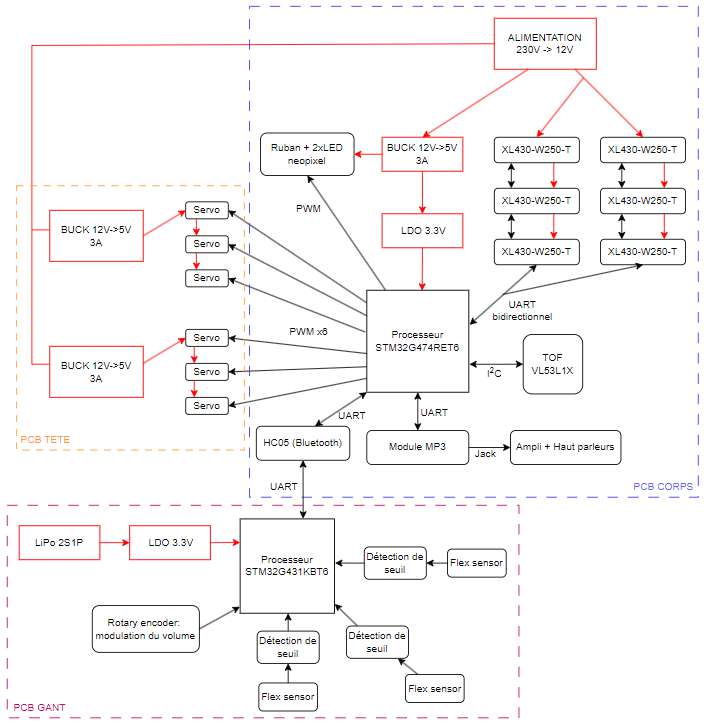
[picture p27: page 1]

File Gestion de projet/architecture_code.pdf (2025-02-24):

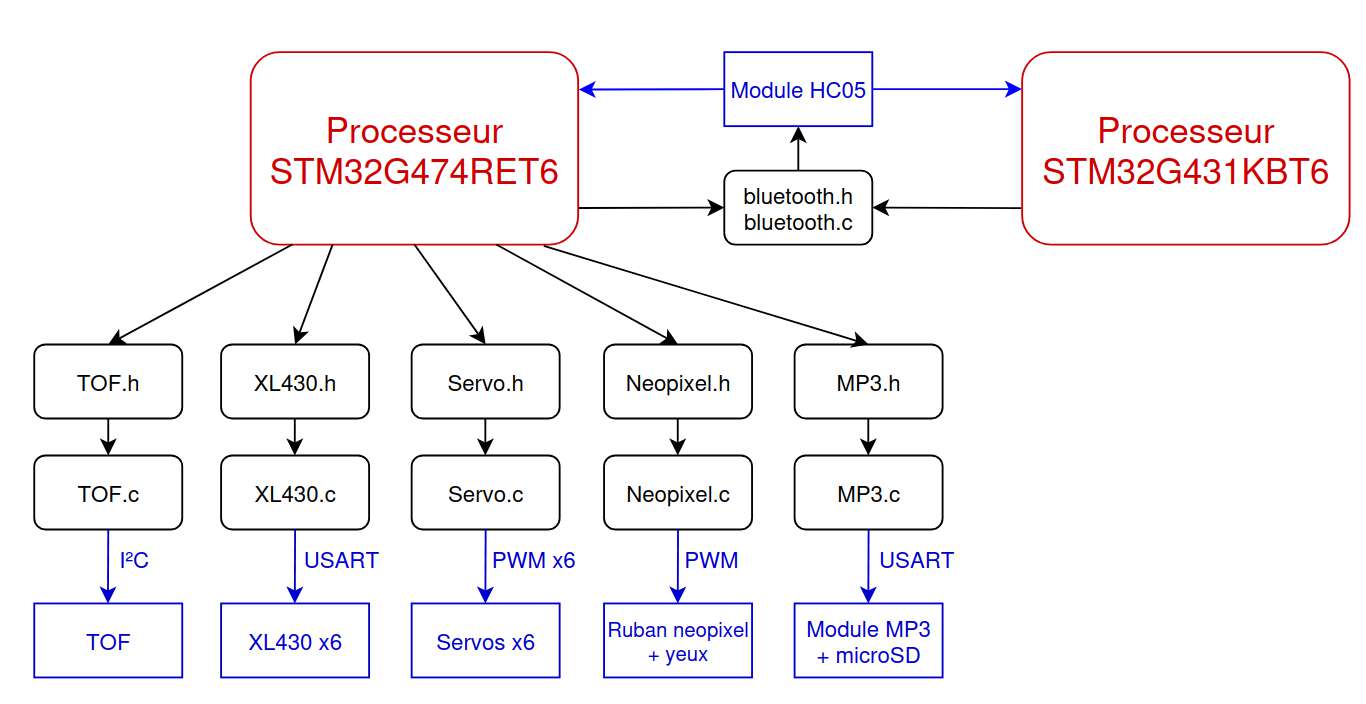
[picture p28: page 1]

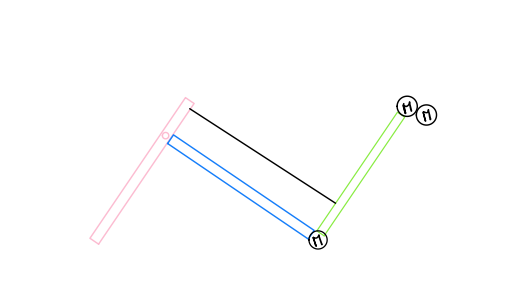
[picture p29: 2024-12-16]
Hardware/Mecanique/ailes/photos/mécanisme ailes aigles.png

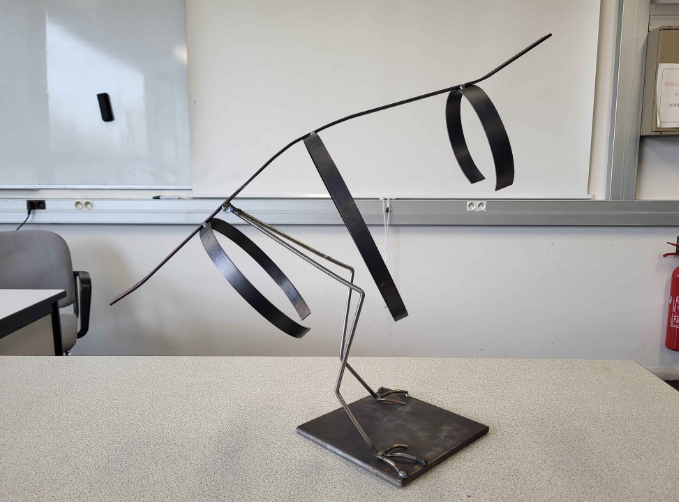
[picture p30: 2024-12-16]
Hardware/Mecanique/ailes/photos/squelette aigle.png

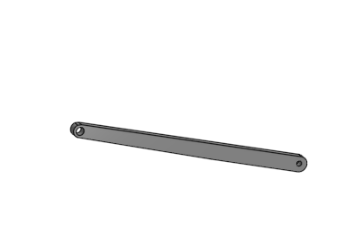
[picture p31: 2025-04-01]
Hardware/Mecanique/head/photos/liaison_bouche.png

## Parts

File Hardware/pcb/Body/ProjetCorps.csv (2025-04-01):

Reference | Value | Datasheet | Footprint | Qty | DNP
C1,C2,C5,C102,C103,C104 | 100n | ~ | Capacitor_SMD:C_0402_1005Metric | 6
C3,C801 | 10n | ~ | Capacitor_SMD:C_0402_1005Metric | 2
C4,C6 | 1u | ~ | Capacitor_SMD:C_0402_1005Metric | 2
C101 | 4u7 | ~ | Capacitor_SMD:C_0402_1005Metric | 1
C106 | 10u | ~ | Capacitor_SMD:C_0402_1005Metric | 1
C107 | 22u | ~ | Capacitor_SMD:C_Elec_5x5.4 | 1
D101,D102,D103 | BLUE_LED | https://www.we-online.com/components/products/datasheet/150060RS55040.pdf | LED_SMD:LED_0603_1608Metric | 3
D104,D105,D106 | RED_LED | https://www.we-online.com/components/products/datasheet/150060RS55040.pdf | LED_SMD:LED_0603_1608Metric | 3
H101,H102,H103,H104 | MountingHole_Pad | ~ | MountingHole:MountingHole_3.2mm_M3_Pad_Via | 4
J1,J3 | Conn_01x04 | ~ | Connector_JST:JST_EH_B4B-EH-A_1x04_P2.50mm_Vertical | 2
J2 | Conn_01x06 | ~ | Connector_JST:JST_EH_B6B-EH-A_1x06_P2.50mm_Vertical | 1
J101 | Conn_01x02 | ~ | Connector_AMASS:AMASS_XT60-M_1x02_P7.20mm_Vertical | 1
J102,J103 | Conn_01x03 | ~ | Connector_JST:JST_EH_B3B-EH-A_1x03_P2.50mm_Vertical | 2
J104 | Conn_01x15 | https://www.we-online.com/components/products/datasheet/618015231421.pdf | libs:CONN15_31321_WRE | 1
J105 | Conn_ST_STDC14 | https://www.st.com/content/ccc/resource/technical/document/user_manual/group1/99/49/91/b6/b2/3a/46/e5/DM00526767/files/DM00526767.pdf/jcr:content/translations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 | Connector_PinHeader_1.27mm:PinHeader_2x07_P1.27mm_Vertical_SMD | 1
R1 | 100k | ~ | Resistor_SMD:R_0805_2012Metric | 1
R101,R102 | 1k | ~ | Resistor_SMD:R_0402_1005Metric | 2
R103,R104,R105 | 82 | ~ | Resistor_SMD:R_0402_1005Metric | 3
R107 | 5k1 | ~ | Resistor_SMD:R_0402_1005Metric | 1
R108 | 1k6 | ~ | Resistor_SMD:R_0402_1005Metric | 1
R109 | 820 | ~ | Resistor_SMD:R_0402_1005Metric | 1
R801,R802 | 10k | ~ | Resistor_SMD:R_0402_1005Metric | 2
SW1,SW801 | SW_SPST | ~ | Button_Switch_SMD:SW_Push_1P1T_NO_6x6mm_H9.5mm | 2
SW101 | SW_SPDT | https://www.we-online.com/components/products/datasheet/472123010111.pdf | mylib:472123010111 | 1
U1 | STM32G474RETx | https://www.st.com/resource/en/datasheet/stm32g474re.pdf | Package_QFP:LQFP-64_10x10mm_P0.5mm | 1
U103 | AZ1117-3.3 | https://www.diodes.com/assets/Datasheets/AZ1117.pdf | Package_TO_SOT_SMD:SOT-223-3_TabPin2 | 1
U104 | 173010542 |  | Library:173010542 | 1

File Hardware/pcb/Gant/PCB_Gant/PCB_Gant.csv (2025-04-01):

Reference | Value | Datasheet | Footprint | Qty | DNP
C1 | 1u | ~ | Capacitor_SMD:C_0402_1005Metric | 1
C2 | 0.1u | ~ | Capacitor_SMD:C_0402_1005Metric | 1
C3 | 10n | ~ | Capacitor_SMD:C_0402_1005Metric | 1
C4 | 4u7 | ~ | Capacitor_SMD:C_0402_1005Metric | 1
C5,C6,C9,C12 | 100n | ~ | Capacitor_SMD:C_0402_1005Metric | 4
C7 | 10u | ~ | Capacitor_SMD:C_0402_1005Metric | 1
C8 | 22u | ~ | Capacitor_SMD:C_Elec_5x5.4 | 1
Flex1neg1,Flex1pos1,Flex2neg1,Flex2pos1,Flex3neg1,Flex3pos1 | TestPoint | ~ | TestPoint:TestPoint_Pad_D1.5mm | 6
H1,H2,H3,H4 | MountingHole_Pad | ~ | MountingHole:MountingHole_3.2mm_M3_Pad_Via | 4
J1 | Conn_ST_STDC14 | https://www.st.com/content/ccc/resource/technical/document/user_manual/group1/99/49/91/b6/b2/3a/46/e5/DM00526767/files/DM00526767.pdf/jcr:content/translations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 | Connector_PinHeader_1.27mm:PinHeader_2x07_P1.27mm_Vertical_SMD | 1
J2 | Conn_01x06 | ~ | Connector_JST:JST_EH_B6B-EH-A_1x06_P2.50mm_Vertical | 1
J3 | Conn_01x02 | ~ | Connector_JST:JST_EH_B2B-EH-A_1x02_P2.50mm_Vertical | 1
R1,R4,R6,R8,R10,R12,R13,R14 | 10k | -- valeurs mixées -- | -- valeurs mixées -- | 8
R2,R7,R11 | 20k | ~ | Resistor_SMD:R_0402_1005Metric | 3
R3,R5,R9 | 4.7k | ~ | Resistor_SMD:R_0402_1005Metric | 3
SW2 | RotaryEncoder | https://www.mouser.lu/datasheet/2/15/EC12E-1370769.pdf | Rotary_Encoder:RotaryEncoder_Alps_EC12E_Vertical_H20mm | 1
U1 | STM32G431KBTx | https://www.st.com/resource/en/datasheet/stm32g431kb.pdf | Package_QFP:LQFP-32_7x7mm_P0.8mm | 1
U2,U3 | MCP602 | http://ww1.microchip.com/downloads/en/DeviceDoc/21314g.pdf | Package_SO:SOIC-8_3.9x4.9mm_P1.27mm | 2
U5 | AZ1117-3.3 | https://www.diodes.com/assets/Datasheets/AZ1117.pdf | Package_TO_SOT_SMD:SOT-223-3_TabPin2 | 1

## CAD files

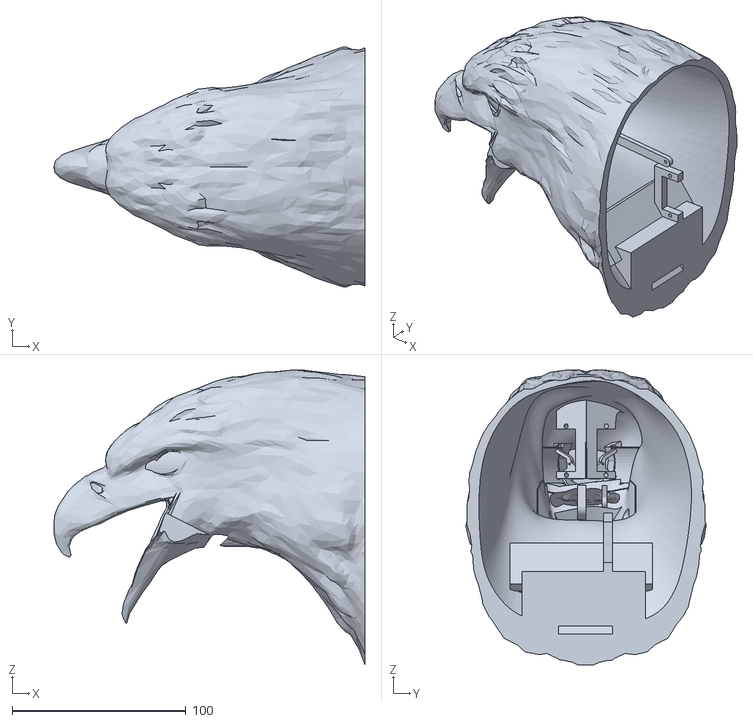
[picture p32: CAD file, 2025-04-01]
Hardware/Mecanique/head/stl/Tete_aigle_full.stl
178.9 x 138.3 x 169.6

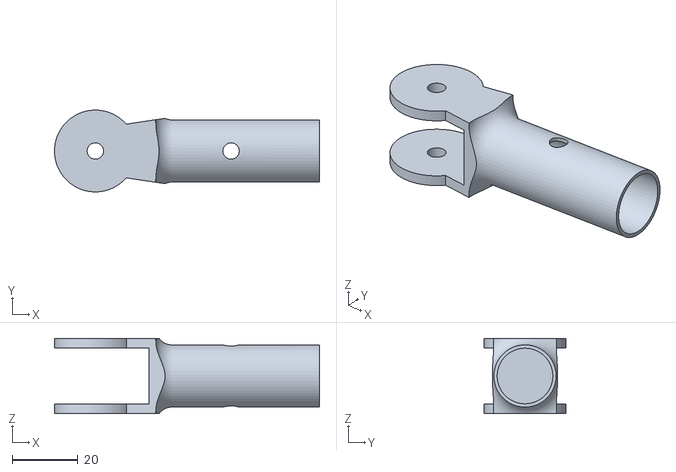
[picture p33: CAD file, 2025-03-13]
Hardware/Mecanique/ailes/3D_print_a_jour/stl/liaison avant-bras - main.stl
80.9 x 25.0 x 23.0

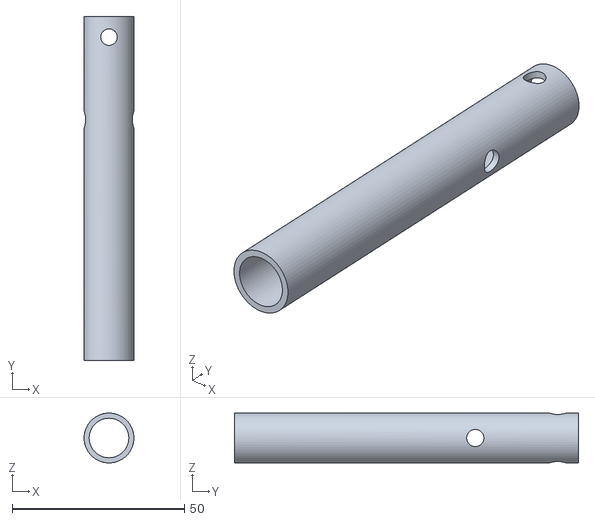
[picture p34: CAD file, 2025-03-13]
Hardware/Mecanique/ailes/3D_print_a_jour/stl/main (1).stl
14.5 x 100.0 x 14.5

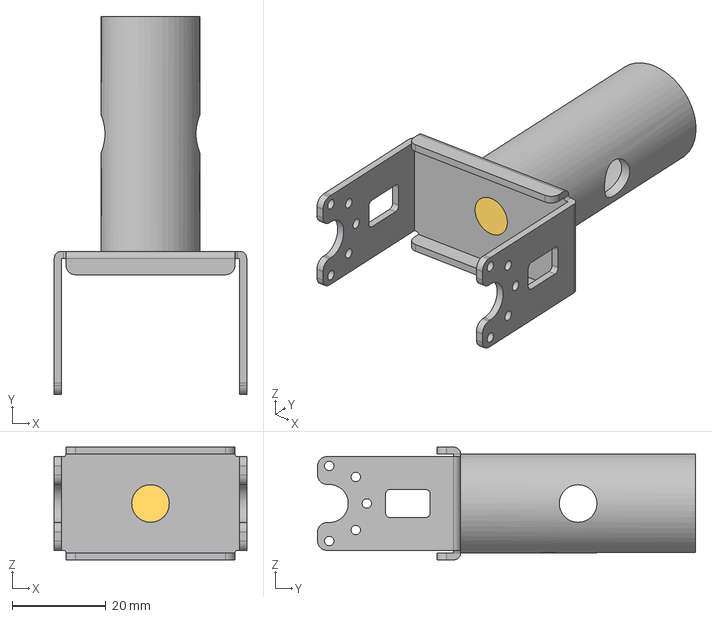
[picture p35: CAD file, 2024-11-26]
Hardware/Mecanique/ailes/3D_print_a_jour/step/liaison coude.step
41.0 x 80.5 x 24.0 mm

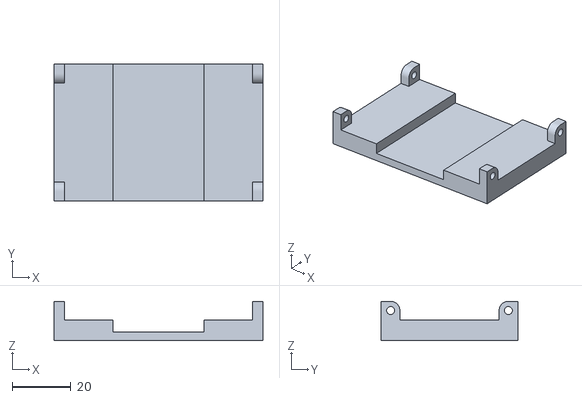
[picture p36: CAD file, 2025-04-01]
Hardware/Mecanique/ailes/3D_print_a_jour/stl/epaule_bas.stl
71.0 x 46.5 x 13.4

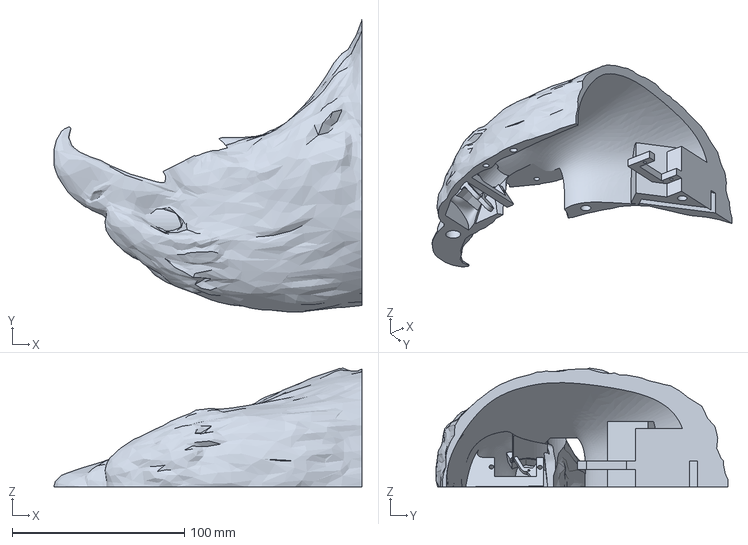
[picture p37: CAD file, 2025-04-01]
Hardware/Mecanique/fichiers stl:3mf/Tete aigle maillage reduit STEP_mouth_left.3mf
178.8 x 169.6 x 69.0 mm

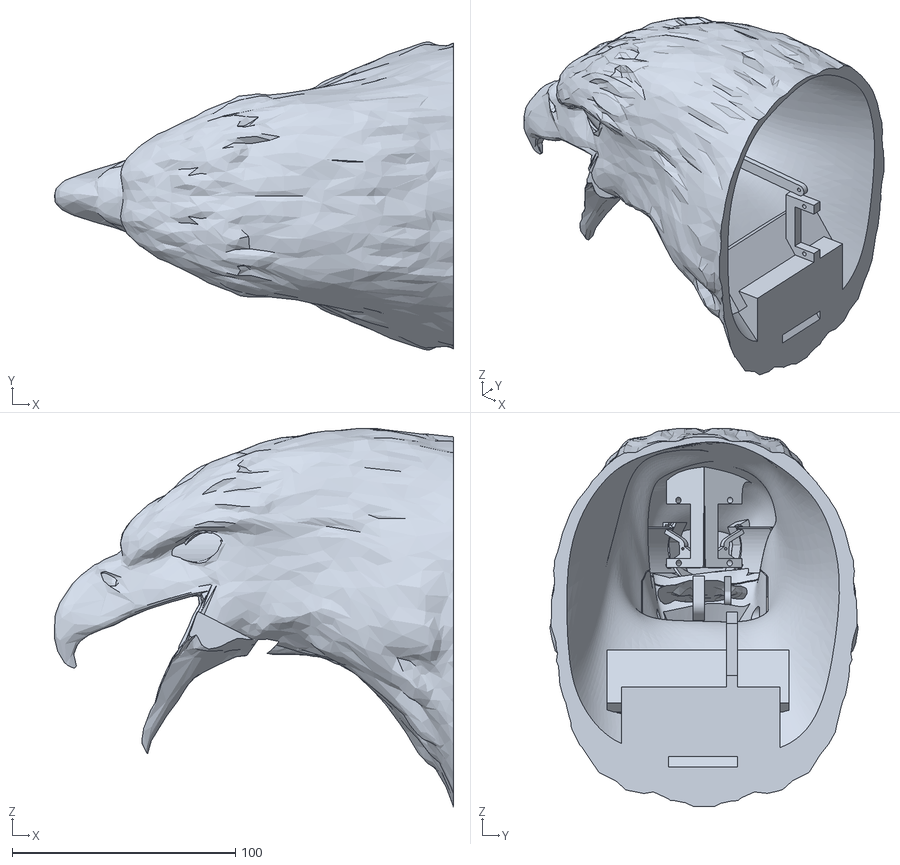
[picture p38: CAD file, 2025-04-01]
Hardware/Mecanique/head/stl/tete_2sides.stl
178.9 x 138.3 x 169.6

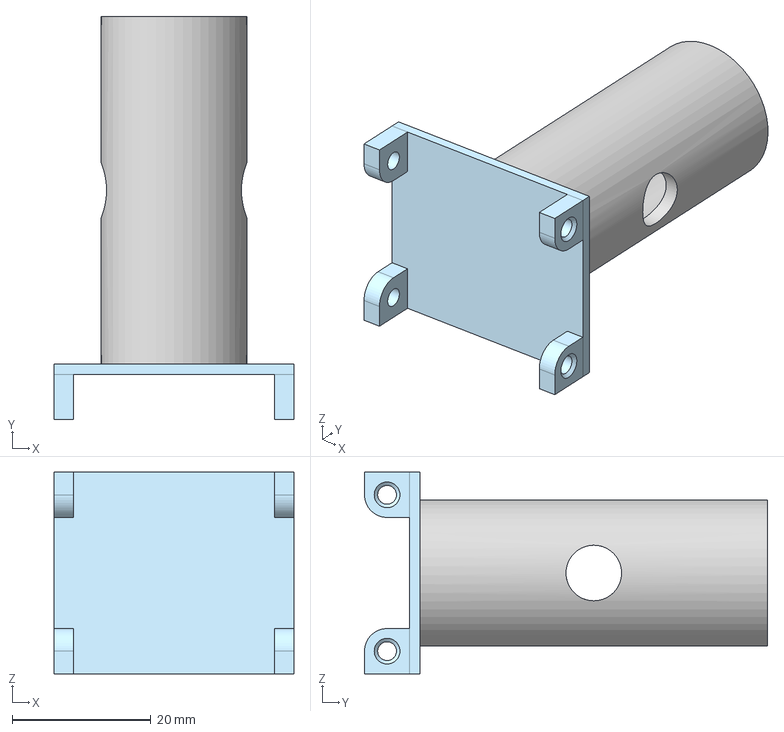
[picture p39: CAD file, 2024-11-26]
Hardware/Mecanique/ailes/3D_print_a_jour/step/liaison moteur.step
34.5 x 58.0 x 29.0 mm

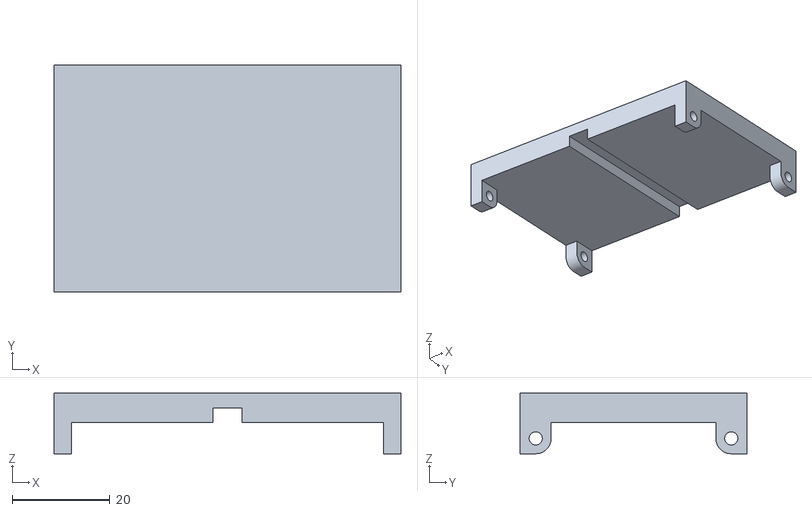
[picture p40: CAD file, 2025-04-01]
Hardware/Mecanique/ailes/3D_print_a_jour/stl/epaule_haut.stl
71.0 x 46.5 x 12.4

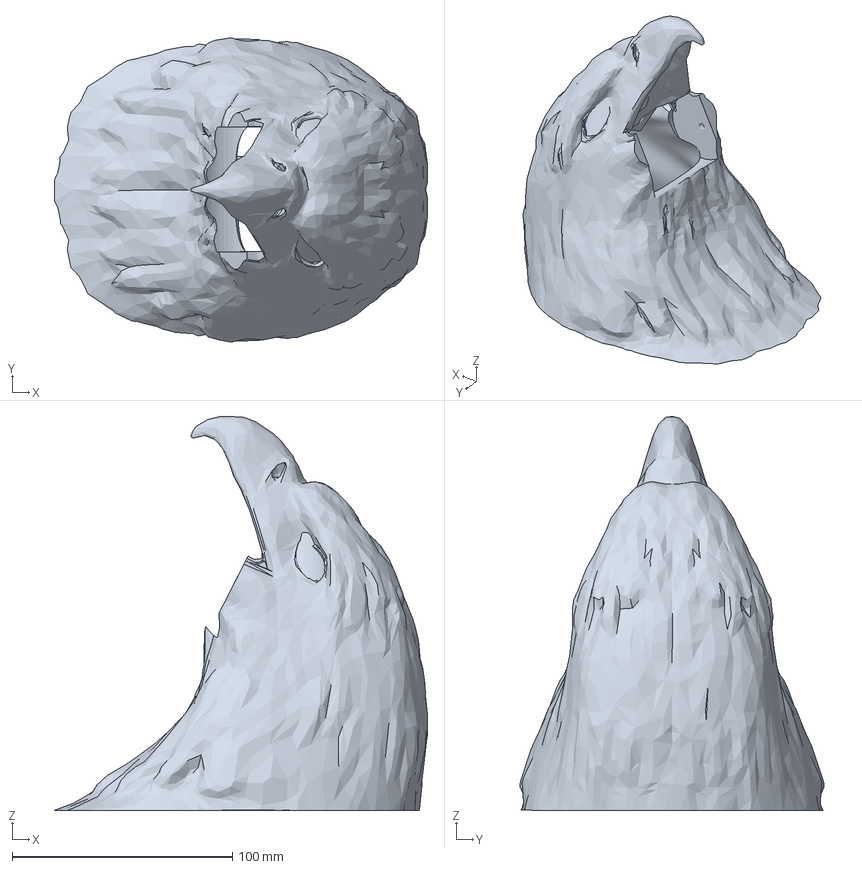
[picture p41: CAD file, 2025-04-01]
Hardware/Mecanique/fichiers stl:3mf/Tete aigle maillage reduit STEP.3mf
169.6 x 138.3 x 178.9 mm

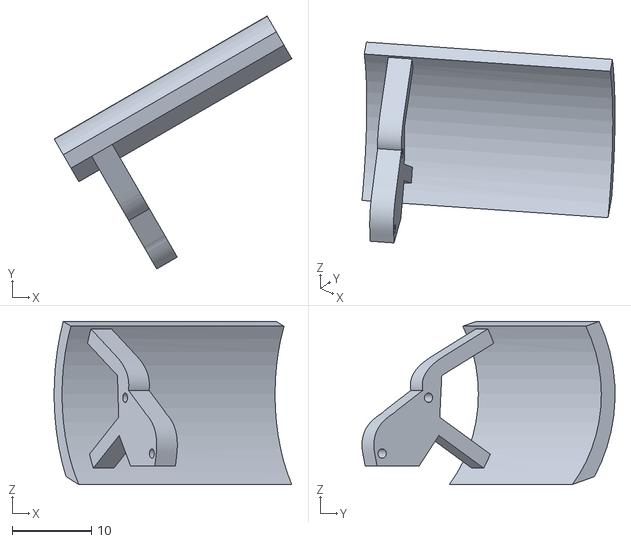
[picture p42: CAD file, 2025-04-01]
Hardware/Mecanique/head/stl/Tete aigle maillage reduit STEP - paupière_left.stl
30.0 x 31.9 x 20.6

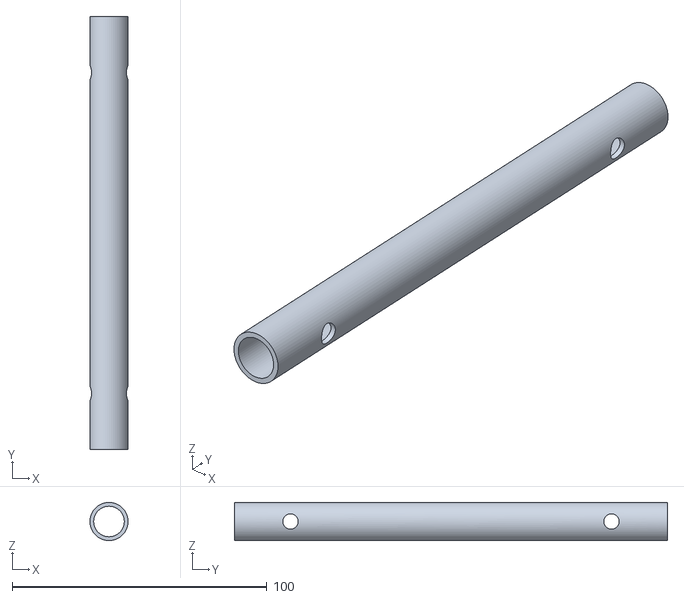
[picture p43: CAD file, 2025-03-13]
Hardware/Mecanique/ailes/3D_print_a_jour/stl/radius (1).stl
15.0 x 170.0 x 15.0

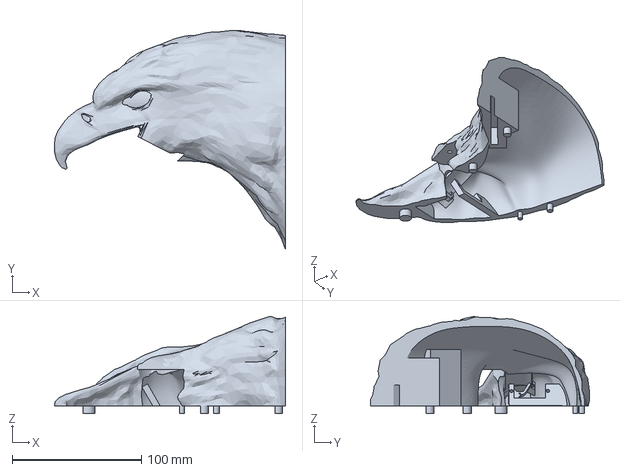
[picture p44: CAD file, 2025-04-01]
Hardware/Mecanique/fichiers stl:3mf/Tete aigle maillage reduit STEP_mouth_right.3mf
178.9 x 169.5 x 75.3 mm

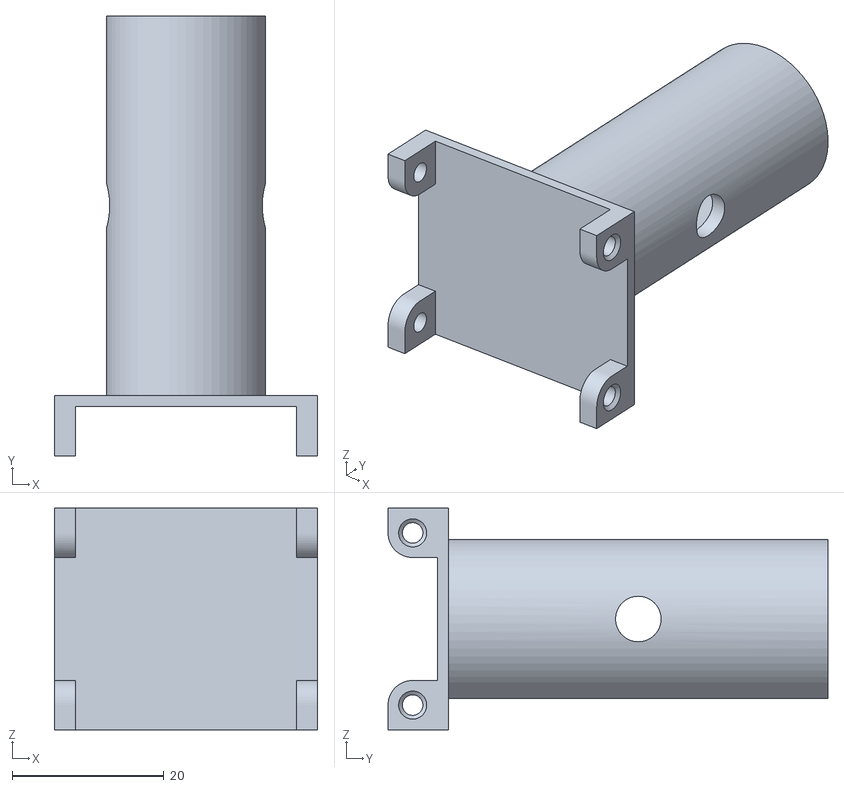
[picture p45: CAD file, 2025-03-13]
Hardware/Mecanique/ailes/3D_print_a_jour/stl/liaison épaule.stl
34.7 x 58.0 x 29.2

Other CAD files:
Hardware/Mecanique/fichiers stl:3mf/partie droite.3mf
Hardware/Mecanique/head/stl/Tete aigle maillage reduit STEP - paupière_right.stl
Hardware/Mecanique/ailes/3D_print_a_jour/stl/humérus (1).stl
Hardware/Mecanique/ailes/3D_print_a_jour/stl/liaison coude.stl
Hardware/Mecanique/fichiers stl:3mf/Tete aigle maillage reduit STEP - Part 3.3mf
Hardware/Mecanique/fichiers stl:3mf/Tete aigle maillage reduit STEP - Part 3.stl
Hardware/Mecanique/fichiers stl:3mf/Tete aigle maillage reduit STEP_mouth.3mf
Hardware/Mecanique/fichiers stl:3mf/partie droite.stl
Hardware/Mecanique/fichiers stl:3mf/partie gauche.stl
Hardware/Mecanique/fichiers stl:3mf/partie gauche.stl#1.cxprj.3mf
Hardware/Mecanique/fichiers stl:3mf/partiedroite.stl
Hardware/Mecanique/head/Blender/untitled.blend

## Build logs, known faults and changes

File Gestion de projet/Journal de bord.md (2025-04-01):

# 2425_Projet2A_Animatronic
Projet ENSEA 2A Animatronic

# DEA : Dynamic Eagle Animatronic

Depuis la Grêce antique et le mythe du géant de bronze Talos, les hommes ont toujours cherchés à créer des automates avec les moyens à leur disposition. Les animatroniques sont l'achèvement actuel de ce désir. Ce sont des poupées mécaniques plus ou moins réalistes dont le fonctionnement interne fait intervenir autant la mécanique que l'électronique.
Elles sont, depuis plusieurs décennies, et encore aujourd'hui principalement utilisées dans le domaine du divertissement au travers des parcs d'attractions, des films et des séries.

Dans le cadre d'un projet de deuxième année à l'école d'ingénieur ENSEA,  nous allons continuer une animatronique d'aigle. Cela sera supervisé par [M.Papazoglou](https://github.com/DBXYD?tab=overview&from=2024-05-01&to=2024-05-29) et [M.Fiack](https://github.com/lfiack).

<table>
  <tr>
    <td>Diagramme d'architecture</td>
    <td>Diagramme d'architecture du code</td>
  </tr>
</table>

[](https://github.com/mael-lukas/2425_Projet2A_Animatronic/blob/main/Gestion%20de%20projet/diagramme_architecture.png)
[](https://github.com/mael-lukas/2425_Projet2A_Animatronic/blob/main/Gestion%20de%20projet/architecture_code.png)

# Equipe
Membres de l'équipe : 
* #### Vincent Fernandes
    * [Github](https://github.com/FernandesVincent)
    * [Linkedin](https://www.linkedin.com/in/vincent-fernandes-0981552a6/)
* #### Maël Lukas
    * [Github](https://github.com/mael-lukas)
    * [Linkedin](https://www.linkedin.com/in/mael-lukas/)
* ##### Romane Ponthieu
    * [Github](https://github.com/Romanepnth)
    * [Linkedin](https://www.linkedin.com/in/romane-ponthieu/)
* #### Sedrenn Labrousse
    * [Github](https://github.com/Sedrennl)
    * [Linkedin](https://www.linkedin.com/in/sédrenn-labrousse-24b2a5295/)

* #### Supervisé par Nicolas Papazoglou
    * [Github](https://github.com/DBXYD?tab=overview&from=2024-05-01&to=2024-05-29)
    * [Linkedin](https://www.linkedin.com/in/nicolas-papazoglou-38382646/?originalSubdomain=fr)
 
* #### Supervisé par Laurent Fiack
    * [Github](https://github.com/lfiack)
    * [Linkedin](https://fr.linkedin.com/in/laurent-fiack-1b1415124)

Nous vous invitons à consulter notre [github de l'année dernière](https://github.com/mael-lukas/2324_Projet1AB_Animatronic), dans lequel vous pourrez trouver toutes les bases sur lesquelles nous avons démarré ce projet.

# TITRE 

Ce projet s'articule autour de plusieurs compétences techniques : informatique, électronique & CAO, modélisation & impression 3D et mécanique.

## Informatique

Cette partie a été majoritairement traitée par Maël avec également, de manière plus minoritaire, Vincent.
Dans cette partie nous allons voir comment tout le code nécessaire au bon fonctionnement du DEA se présente.

## Électronique & CAO

Cette partie concerne différentes sous compétences : la conception des PCB et la soudure de ceux-ci, les test associés et finalement le cablâge. 
Comme notre projet inclus plusieurs PCB, la conception des PCB a été faite par Vincent (PCB du corps et du gant) et Romane (PCB de la tête).
Les soudures CMS ont été réalisées par Maël et Romane, tandis que les soudures THT ont été réalisées par Vincent.
Le cablâge (sertissage) a été réalisé par Vincent.

## Modélisation & Impression 3D

Cette partie a été essentiellement traitée par Sedrenn aidée de Romane et Vincent.

## Mécanique

Cette partie concerne la gestion des différents moteurs qui a été faite par Maël pour l'implémentation du code, par Vincent pour le cablâge de ceux ci et leur placement sur la structure de l'aigle et par Sedrenn et Romane pour la conception des pièces 3D permettant de faire les liaisons entre ceux ci.

### expliquer de manière à faire en sorte que anyone puisse le refaire chez soi
# nezodnzeonroze

Pour commencer, veuillez trouver ci-dessous le diagramme d'architecture qui nous a servis de base pour la création des PCB de ce projet:

Voici donc, le schematic et le routage du PCB principal de projet, le PCB du corps :

Ce PCB a eu le droit à plusieurs versions afin de l'améliorer à chaque ittération. La dernière en date est l'ajout de R1, une résistance de pull-up pour le protocol UART qui nous sert à commander les moteurs. Cependant, une fois ce nouveau PCB soudé et testé nous n'arrivions plus à communiquer avec les moteurs donc nous sommes repassé sur la version antérieure du PCB, qui elle est foncitonnel, où la résistance de pull-up est activée sur STM32CubeIDE.
Vous pouvez trouvez [ici]() la BOM de ce PCB.

Le second PCB que nous avons du réalisé est celui de la tête, vous constaterez qu'il n'a pas changé depuis [l'année dernière]() voici donc simplement son schematic, son routage et sa BOM.

Il est à noter qu'avec plus de temps nous aurions suremenent modifier ce PCB car les besoins de notre projet ont changés, nous n'avons plus besoin de contrôler six servomoteurs mais par contre nous avons besoin d'une piste GPIO pour contrôler l'état haut ou bas de la pin XSDN du TOF.

Le troisième et dernier PCB de projet est le PCB du gant qui se présente comme suit :
(schematic, Routage et BOM)

L'objectif avec ce PCB est de pouvoir commandé les mouvements de l'aigle avec les mouvements de nos doigts et ce sans liaison filaire mais avec une liaison bluetooth grâce au module HC05. Les empreintes de résistances en 1206 correspondent aux pads pour les [flex sensors]() qui sont des résistances variables qui nous permmettent grâce aux circuits visibles sur le schematic d'avoir une tension seuil à partir de laquelle on peut activer tel ou tel mouvement de l'aigle.
Pour pouvoir fonctionner via une liaison Bluetooth nous alimentons le PCB grâce à une batterie Li-ion 1S et grâce à un module servant de Boost pour pouvoir amener une tension de +5V au pcb.

Ce PCB pourrait avoir des versions plus évoluées notamment vis à vis des circuits des flex sensors qui peuvent être largement améliorer afin de par exemple pouvoir changer la tension seuil désirée avec des potentiomètres à la place des résistances.

Ce PCB permet également le contrôle du volume du haut parleur grâce au rotary encoder présent dessus. Pour revenir rapidement sur cette partie "haut parleur", l'objectif est de pouvoir jouer des sons grâce à un parleur présents entre les pattes de l'aigle en fonction de la distance avec la personne en face de lui grâce au TOF. Par exemple, si je me trouve à un mètre de l'oiseau il me dira "Bonjour" par contre si je m'approche à dix centimètres de celui-ci il me dira "Recule".

Pour finir cette partie, vous pouvez voir ci-dessous quelques photos des PCB réaliés. Vous constaterez qu'ils sont chacun entourés d'un support fait en impression 3D. Ces supports ne sont pas nécessaire in fine mais ils permettent d'éviter les risques en empéchant les collisions malheureuses entre les PCB, ce qui pourrait amener des problèmes si cela se passe lorsqu'ils sont en fonctionnement.

Maintenant que nous avons commencé à parler de modélisation 3D il est temps d'attaquer le gros de celle-ci. En effet, nous avons décidés d'imprimer l'aigle entièrement en 3D en le vidant bien sûr à l'intérieur afin de pouvoi y plcer notre matériel. Nous avons séparés cette modélisation en 3 parties : la tête, les ailes et le reste.

Tout d'abord, la tête:
C'est sans aucun doute la partie la plus compliquée de cette modélisation car il faut la travailler pour faire en sorte que le bec et les paupières de l'aigle soit amovibles et contrôlables par des servomoteurs. Voici, ci-dessous les modèles 3D et l'impression de celle-ci.

Pour continuer, les ailes: 
À l'opposé de la tête, c'est la modééisation la plus simple de projet car elle consiste seulement en la réalisation de pièces permettant d'approximer les os de l'aigle avec des emplacements pour les moteurs de l'épaule et du coude. À cela il faut ajouter les modules rouges que vous pourrez voir ci-après qui permettent la pose des plumes.

Pour finir, le corps:
Au vu du temps disponible, nous avons juste eu le temps de travailler la cage toracique de l'oiseau et donc nous avons délaissé la queue et les pattes qui n'ont pas d'autres utilités à part apporter de l'esthétique au projet, là où l'abdomen possède, lui, un réel intérêt. En effet, il nous permet de ranger à l'intérieur l'ensemble de notre électronique et de notre câblage afin que le projet ne laisse, dans l'idéal, rien apparaître de l'extérieur si tenté un câble d'alimentation.

La modélisation du courps à du se faire en quatres parties car nous avions une coontrainte de temps : les impressiosns ne peuvent pas durer plus de 12h et les dimensions des imprimantes 3D qui sont trop petites pour notre modélisation. En effet, les plus grandes imprimantes 3D que nous pssédons sont des Creality K1 Max qui permettent de réaliser des impressions en 300x300x300 or le corps de l'oiseau tend plutôt sur du 350x400x200. De plus, pour l'assemblage de ces quatres parties, au vu du temps mis à disposition pour ce projet nous n'avons pas pu prévoir de moyen d'emboîter et de désemboiter cette partie. Pour que le tout se tienne nous avons donc pris le partit de souder entre eux les morceaux de PLA une fois imprimés.

Nous avons rapidement abordé la question des moteurs dans la partie précédente mais pour l'aborder un peu plus en profondeur, nous utilisons deux références de moteurs pour ce projet, les FS90 et les XL430. Les premiers sont des servomteur 180° permettant le choix d'une position sur un plage de 180° par l'envoi d'une PWM. Nous les utilisons pour commander le bec et les yeux de l'aigle car cela ne requiert que par de force. De l'autre côté, les XL430 nous servent pour les mouvement plus complexes et surtout qui demandent plus de force. En effet, nous utilisons six de ces moteurs pour réaliser les ailes de l'oiseau, sur chaque aile nous avons deux XL430 qui sont utilisés pour reproduire l'épaule et le troisième pour reproduire ce que nous pourrions appeler le coude. 

Vous l'avez peut-être remarquez sur les photos ci-dessus mais toutes les pièces liants les XL430 ont été réalisées en impression 3D à l'exceptio de la pièce liant les deux moteurs de l'épaule. En effet, nous avions également fait une première version de cette pièce en impression 3D mais le problème était qu'elle doit pouvoir soutenir tout le poids de l'aile. Cela a causé la destruction de la version 3D de la pièce lorsqu'i fallut tester les mouvements de l'aile. Pour pallier à cela nous avons commander la pièce en métal aurpès du fournisseur et c'est donc cette pièce que vous pouvez voir sur les photos.

Cependant, tout cela ne pourrait pas fonctionner sans code. Voici, ci-dessous le diagramme d'architecture du code:

Nous allons traiter chaque partie de code de gauche à droite d'après ce diagramme en commençant tout d'abord par le code pour la communication bluetooth entre le STM32G474RET6 et le STM32G431KBT6.

Il faut cependant noter que nous n'avons cependant pas eu le temps de le tester correctement.

Pour le code du TOF, cette partie a été particulièrement compliquée pour nous et avions finis par la laisser un peu de côté au profit d'autres parties mais finalement nous avons pu avoir accès à une librairie écrite par M. Fiack et disponible sur son github. En adaptant cette librairie au processeur que nous utilisons nous avons pu faire fonctionner le TOF correctement. 

Les XL4430 sont sans aucun doute la partie la plus complexe de tout le projet, même au bout de tant de temps à travailler dessus nous avons toujours des problèmes dont nous ne comprenons pas la présence. En particulier, lorsque l'exact même code fonctionnait une semaine auparavant.

Les LED neopixel sont quant à elles une partie assez simple que nous avions réussi à faire fonctionner par l'envoi de PWM avant de passer à une version plus avancée grâce à une librairie de M. Fiack qui utilise le DMA.

Finalement, le code du module est surement la partie qui nous a été le plus simple à réalisée et qui nous permet, avec le module suivant : https://www.gotronic.fr/art-module-mp3-uart-mp3player-38215.htm de pouvoir jouer n'importe quel son présent sur la carte micro SD.

# Journal de bord

## Séance 1
   Cette séance étant la première, elle nous a servit à définir les nouveaux objectifs de notre projet : nous voulons finaliser complètement notre aigle, c'est-à-dire finir la modélisation 3D, et finir le code. De plus, nous voulons ajouter des nouvelles fonctionnalités à notre aigle : nous voulons le faire crier en fonction de la distance de l'utilisateur, et nous voulons qu'il s'illumine. Pour y voir plus clair, nous avons effectué une première version du diagramme d'architecture. Afin de nous organiser au mieux au vu du temps disponible pour ce projet, nous nous sommes directement répartit différentes tâches à réaliser durant les semaines qui suivent.
   * #### Modélisation 3D de l'aigle
        * [Sedrenn](https://github.com/mael-lukas/2324_Projet1AB_Animatronic/tree/main?tab=readme-ov-file#sedrenn-labrousse)
   * #### Programmation 
        * [Maël](https://github.com/mael-lukas/2324_Projet1AB_Animatronic/tree/main?tab=readme-ov-file#ma%C3%ABl-lukas)
   * #### Conception des différents PCB
        * [Romane](https://github.com/mael-lukas/2324_Projet1AB_Animatronic/tree/main?tab=readme-ov-file#romane-ponthieu)
        * [Vincent](https://github.com/mael-lukas/2324_Projet1AB_Animatronic/tree/main?tab=readme-ov-file#vincent-fernandes)

## Séance 2
   Durant cette séance nous avons affiné notre diagramme d'architecture.

   Nous avons repris les PCB que nous avions conçus l'année dernière, nous en avions 3. Nous avons commencé à chercher aux solutions que nous allons utiliser pour pouvoir effectuer toutes les fonctionnalités que nous voulons avec notre aigle. Nous avons cherché les composants dont nous allons avoir besoin par la suite afin d'effectuer une commande pour tous les composants dont nous ne disposons pas à l'école. 
   Pendant ce temps, [Sedrenn](https://github.com/mael-lukas/2324_Projet1AB_Animatronic/tree/main?tab=readme-ov-file#sedrenn-labrousse) a avancé sur la modélisation 3D et [Maël](https://github.com/mael-lukas/2324_Projet1AB_Animatronic/tree/main?tab=readme-ov-file#ma%C3%ABl-lukas) a continué le code qu'il avait commencé l'année dernière.

## Séance 3
   À cette étape du projet nous avons choisis de changer de microprocesseur, afin d'en utiliser un ayant assez de PIN pour effectuer toutes les fonctionnalités que nous souhaitons. Nous avons donc commencé à concevoir les nouveaux PCB dont nous allons avoir besoin en fonction de ce microprocesseur.
  En parallèle de cela, [Maël](https://github.com/mael-lukas/2324_Projet1AB_Animatronic/tree/main?tab=readme-ov-file#ma%C3%ABl-lukas) a continué le code des moteurs qu'il avait commencé et [Sedrenn](https://github.com/mael-lukas/2324_Projet1AB_Animatronic/tree/main?tab=readme-ov-file#sedrenn-labrousse) a commencé à concevoir le squelette de l'animatronic.

## Séance 4
   Cette séance a permis la finalisation des schematic des 3 [PCB](https://github.com/mael-lukas/2324_Projet1AB_Animatronic?tab=readme-ov-file#pcb) crées sous Kicad et ainsi le passage à l'étape PCB editor pour les membres affectés à cette partie du projet.
   Pendant ce temps [Maël](https://github.com/mael-lukas/2324_Projet1AB_Animatronic/tree/main?tab=readme-ov-file#ma%C3%ABl-lukas) a finalisé une première version du code des moteurs XL430 et [Sedrenn](https://github.com/mael-lukas/2324_Projet1AB_Animatronic/tree/main?tab=readme-ov-file#sedrenn-labrousse) a continué de concevoir le squelette de l'aigle.

## Séance 5
   Durant cette séance, nous avons effectuer une première présentation du projet à nos professeurs, qui ont pu constater notre avancée et nous guider.
   Par la suite, M.Papazoglou et M. Fiack ont pu vérifier les 3 [PCB](https://github.com/mael-lukas/2324_Projet1AB_Animatronic?tab=readme-ov-file#pcb) et nous faire des retours pour que l'on puisse corriger nos erreurs et effectuer des nouvelles modifications.
   M. Fiack a aussi revu les codes des moteurs avec [Maël](https://github.com/mael-lukas/2324_Projet1AB_Animatronic/tree/main?tab=readme-ov-file#ma%C3%ABl-lukas) et il a pu corriger tous les problèmes qu'il rencontrait.
    Pendant cette séance, Sedrenn a pu finir le squelette de l'aigle.
   
   ![Squelette de l'aigle] (../Hardware/Mécanique/ailes/photos/squelette aigle.png)

## Séance 6
   Au cours de cette séance nous avons reçu les commandes de composants ainsi que les PCB.  [Vincent](https://github.com/mael-lukas/2324_Projet1AB_Animatronic/tree/main?tab=readme-ov-file#vincent-fernandes) et [Romane](https://github.com/mael-lukas/2324_Projet1AB_Animatronic/tree/main?tab=readme-ov-file#romane-ponthieu) ont donc pu soudé les PCB durant ces 4 heures.
   En parralèle à cela, [Sedrenn](https://github.com/mael-lukas/2324_Projet1AB_Animatronic/tree/main?tab=readme-ov-file#sedrenn-labrousse) a commencé à modéliser des liaisons permettant de fixer les moteurs qui vont faire bouger les ailes sur le squelette.
  [Maël](https://github.com/mael-lukas/2324_Projet1AB_Animatronic/tree/main?tab=readme-ov-file#ma%C3%ABl-lukas), quant à lui, a commencé le code permettant de programmer le ruban néopixel.

## Séance 7
   Au cours de cette séance, nous avons effectuer une deuxième présentation du projet à M. Papazoglou et M. Fiack, dans lequel nous avons fait un point sur ceque nous avions fini et cequ'il nous restait à faire. 
   Ensuite, [Romane](https://github.com/mael-lukas/2324_Projet1AB_Animatronic/tree/main?tab=readme-ov-file#romane-ponthieu) et [Vincent](https://github.com/mael-lukas/2324_Projet1AB_Animatronic/tree/main?tab=readme-ov-file#vincent-fernandes) se sont réorientés sur de nouveaux sujets : Romane va aider [Sedrenn](https://github.com/mael-lukas/2324_Projet1AB_Animatronic/tree/main?tab=readme-ov-file#sedrenn-labrousse) pour la modélisation 3D de l'aigle et Vincent va s'occuper du code du TOF.
   
   Pendant ce temps [Sedrenn](https://github.com/mael-lukas/2324_Projet1AB_Animatronic/tree/main?tab=readme-ov-file#sedrenn-labrousse) a imprimé une première liaison moteur-squelette et l'a testée par la suite. [Maël](https://github.com/mael-lukas/2324_Projet1AB_Animatronic/tree/main?tab=readme-ov-file#ma%C3%ABl-lukas) a continué le code du ruban néopixel, en effectuant des premiers tests.

<table>
  <tr>
    <td>liaison moteur-squelette</td>
</table>

## Séance 8
   Au cours de cette séance, [Vincent](https://github.com/mael-lukas/2324_Projet1AB_Animatronic/tree/main?tab=readme-ov-file#vincent-fernandes) a continué le code permettant de faire fonctionner le TOF et [Maël](https://github.com/mael-lukas/2324_Projet1AB_Animatronic/tree/main?tab=readme-ov-file#ma%C3%ABl-lukas) l'a aidé avant de commencer l'écriture du code pour le module mp3. Ils ont pu commencé à tester le code du TOF.
   D'un autre côté, [Sedrenn](https://github.com/mael-lukas/2324_Projet1AB_Animatronic/tree/main?tab=readme-ov-file#sedrenn-labrousse) et [Romane](https://github.com/mael-lukas/2324_Projet1AB_Animatronic/tree/main?tab=readme-ov-file#romane-ponthieu) ont réfléchi à un mécanisme permettant d'effectuer les mouvements de l'aigle d'un aigle et elles sont arrivées au schéma ci-dessous.

 <table>
  <tr>
    <td>mécanisme ailes aigles</td>
  </tr>
</table>

## Séance 9
  Durant cette séance, [Sedrenn](https://github.com/mael-lukas/2324_Projet1AB_Animatronic/tree/main?tab=readme-ov-file#sedrenn-labrousse) et [Romane](https://github.com/mael-lukas/2324_Projet1AB_Animatronic/tree/main?tab=readme-ov-file#romane-ponthieu) ont modélisé chaque pièce permettant de concevoir l'articulation de l'aile de l'aigle. 
  Pendant ce temps, [Maël](https://github.com/mael-lukas/2324_Projet1AB_Animatronic/tree/main?tab=readme-ov-file#ma%C3%ABl-lukas) et [Vincent](https://github.com/mael-lukas/2324_Projet1AB_Animatronic/tree/main?tab=readme-ov-file#vincent-fernandes) ont pu faire fonctionner le TOF.

## Séance 10
   
   Au cours de cette séance, nous avons présenter notre avancement à M. Fiack et M. Papazoglou. 
   Ensuite, [Vincent](https://github.com/mael-lukas/2324_Projet1AB_Animatronic/tree/main?tab=readme-ov-file#vincent-fernandes) et [Maël](https://github.com/mael-lukas/2324_Projet1AB_Animatronic/tree/main?tab=readme-ov-file#ma%C3%ABl-lukas) ont pu continué de tester leur code respectif et les modifier en fonction des problèmes qu'ils rencontraient. 
   Pendant ce temps, [Sedrenn](https://github.com/mael-lukas/2324_Projet1AB_Animatronic/tree/main?tab=readme-ov-file#sedrenn-labrousse) et [Romane](https://github.com/mael-lukas/2324_Projet1AB_Animatronic/tree/main?tab=readme-ov-file#romane-ponthieu) ont continué de modéliser les pièces comprises dans l'articulation de l'aile de l'aigle.

<table>
  <tr>
    <td>humérus</td>
    <td>liaison cubitus-main</td>
    <td>liaison coude</td>
  </tr>
</table>

## Séance 11
   
   Au cours de cette dernière séance, [Vincent](https://github.com/mael-lukas/2324_Projet1AB_Animatronic/tree/main?tab=readme-ov-file#vincent-fernandes) et [Maël](https://github.com/mael-lukas/2324_Projet1AB_Animatronic/tree/main?tab=readme-ov-file#ma%C3%ABl-lukas) ont pu finalisé leurs codes et s'assuerer qu'ils fonctionnaient comme ils l'avaient prévus notamment le module MP3 qui, relié à un câble jack dénudé et serti pour s'adapter au connecteur de l'amplificateur du haut-parleur, a permis de jouer un son pré enregistré sur une micro carte SD.
   Pendant ce temps, [Sedrenn](https://github.com/mael-lukas/2324_Projet1AB_Animatronic/tree/main?tab=readme-ov-file#sedrenn-labrousse) et [Romane](https://github.com/mael-lukas/2324_Projet1AB_Animatronic/tree/main?tab=readme-ov-file#romane-ponthieu) ont terminé de modéliser les pièces comprises dans l'articulation de l'aile de l'aigle et ont pu commencéà les imprimer en 3D.

<table>
  <tr>
    <td>liaison moteurs</td>
    <td>radius</td>
  </tr>
</table>

## Conclusion

   Pour conclure la première partie de ce projet, nous n'avons pas encore ce que nous espérons obtenir à la fin, mais nous nous en rapprochons. Chaque partie du projet a considérablement avancé, et certaines sont déjà finalisées, comme les PCB. Il ne nous manque plus que des détails, c'est-à-dire finaliser complètement les codes et effectuer l'assemblage mécanique de l'aigle. Après cela, nous pourrons relier chacune des parties de notre projet et voir si notre animatronique fonctionne comme nous l'avions prévu. Cette étape va être importante, et nous aurons sûrement de nouvelles modifications à effectuer au niveau du code et de la modélisation 3D. 
   L'ensemble du groupe est fier et heureux d'avoir réussi à avancer sur ce projet et il ne s'arrête pas ici puisque nous allons continuer de travailler sur celui-ci durant notre second semestre à l'école.
   Nous avons déjà des idées de projets annexes reliés à notre aigle, par exemple, nous aimerions concevoir un gant permettant de relier le mouvement d'une main d'un utilisateur à celui des ailes de l'aigle.

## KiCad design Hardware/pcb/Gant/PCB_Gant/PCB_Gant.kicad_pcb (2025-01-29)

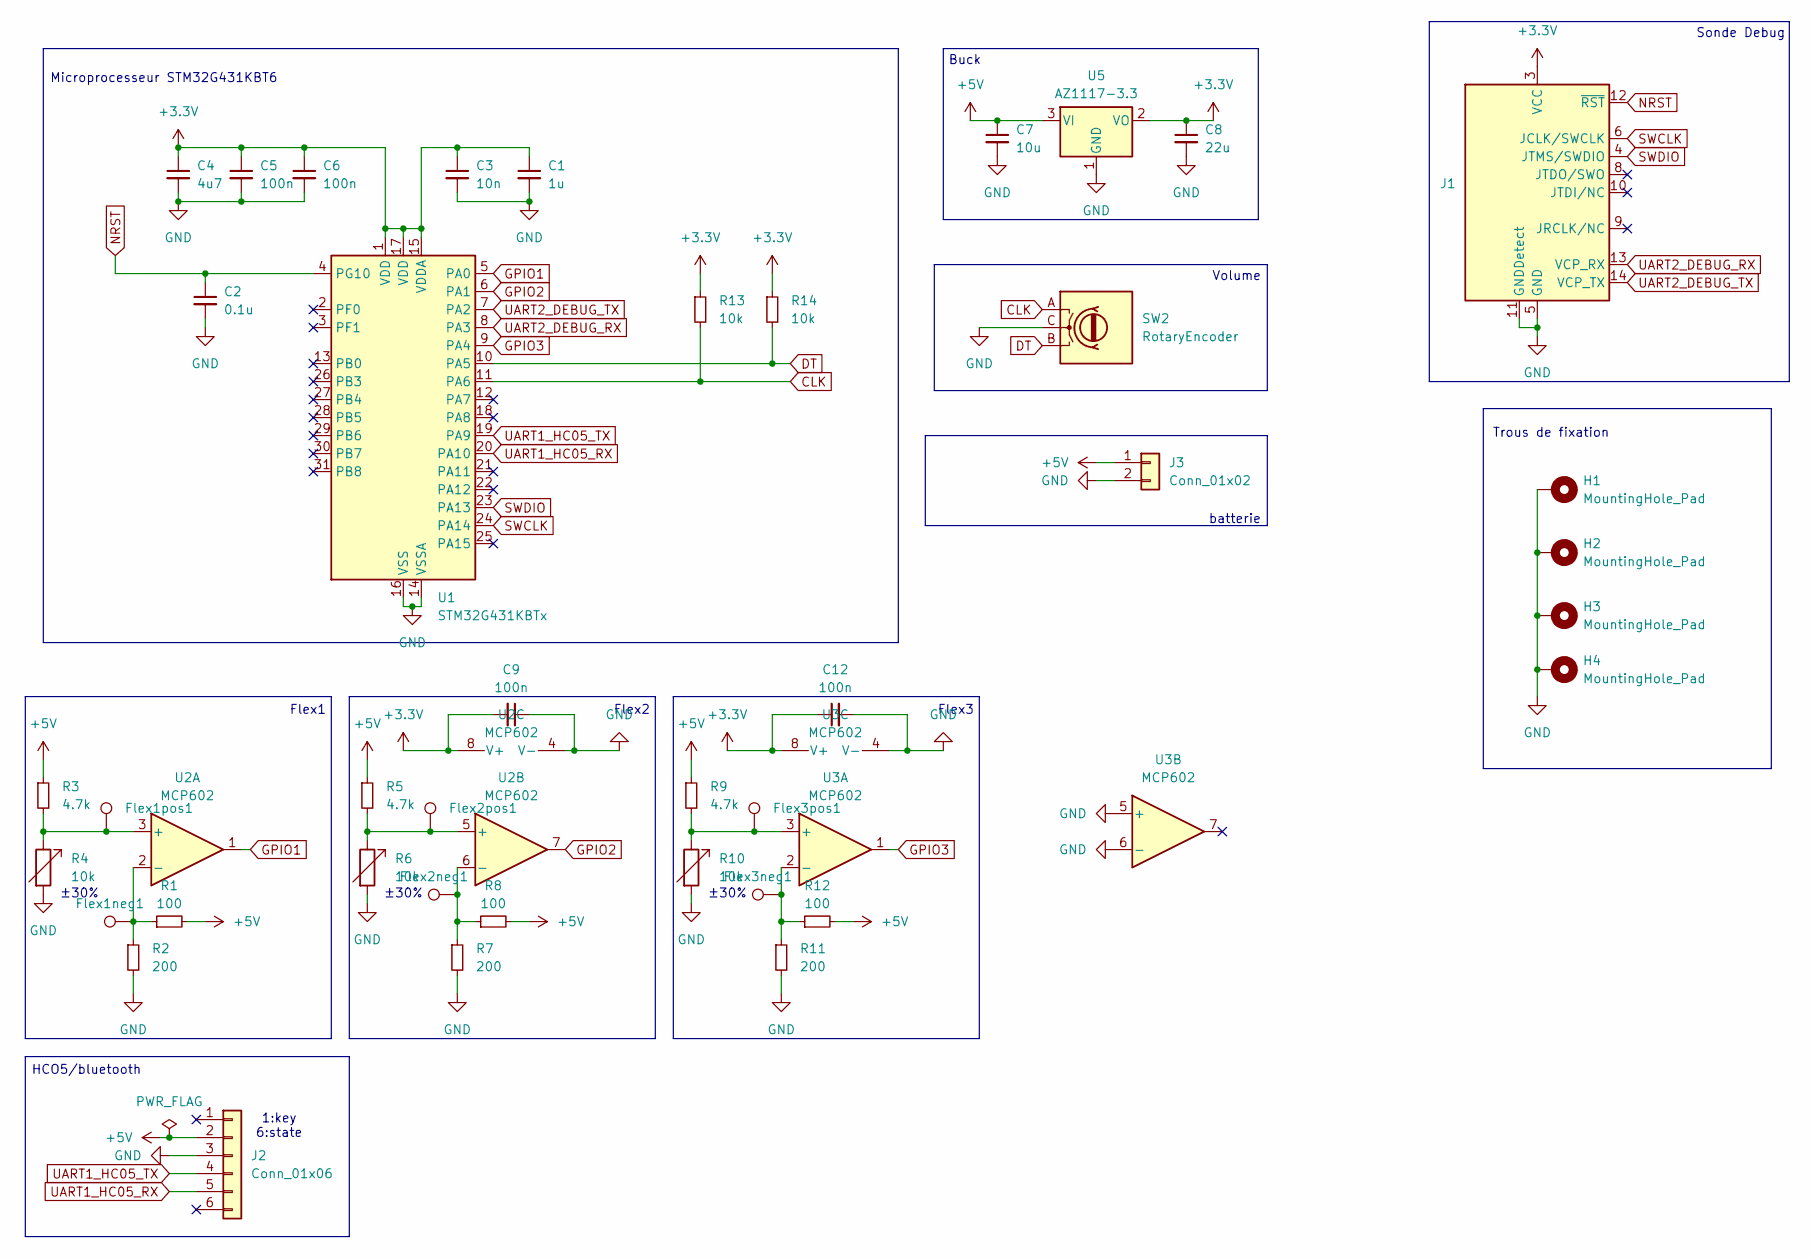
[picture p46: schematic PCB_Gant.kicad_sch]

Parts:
C1: 1u; C_0402_1005Metric
C2: 0.1u; C_0402_1005Metric
C3: 10n; C_0402_1005Metric
C4: 4u7; C_0402_1005Metric
C5, C6, C9, C12: 100n; C_0402_1005Metric
C7: 10u; C_0402_1005Metric
C8: 22u; C_Elec_5x5.4
Flex1neg1, Flex1pos1, Flex2neg1, Flex2pos1, Flex3neg1, Flex3pos1: TestPoint; TestPoint_Pad_D1.5mm
H1, H2, H3, H4: MountingHole_Pad; MountingHole_3.2mm_M3_Pad_Via
J1: Conn_ST_STDC14; PinHeader_2x07_P1.27mm_Vertical_SMD
J2: Conn_01x06; JST_EH_B6B-EH-A_1x06_P2.50mm_Vertical
J3: Conn_01x02; JST_EH_B2B-EH-A_1x02_P2.50mm_Vertical
R1, R8, R12: 100; R_0402_1005Metric
R2, R7, R11: 200; R_0402_1005Metric
R3, R5, R9: 4.7k; R_0402_1005Metric
R4, R6, R10: 10k; R_2512_6332Metric
R13, R14: 10k; R_0402_1005Metric
SW2: RotaryEncoder; RotaryEncoder_Alps_EC12E_Vertical_H20mm
U1: STM32G431KBTx; LQFP-32_7x7mm_P0.8mm
U2, U3: MCP602; SOIC-8_3.9x4.9mm_P1.27mm
U5: AZ1117-3.3; SOT-223-3_TabPin2; MPN AZ1117CH2-3.3TRG1

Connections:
+3.3V: C1.1, C3.1, C4.1, C5.1, C6.1, C8.1, C9.2, C12.1, J1.3 (VCC), R13.1, R14.1, U1.1 (VDD), U1.15 (VDDA), U1.17 (VDD), U2.8 (V+), U3.8 (V+), U5.2 (VO)
+5V: C7.1, J2.2, J3.1, R1.2, R3.1, R5.1, R8.2, R9.1, R12.2, U5.3 (VI)
CLK: R13.2, SW2.A, U1.11 (PA6)
DT: R14.2, SW2.B, U1.10 (PA5)
GND: C1.2, C2.2, C3.2, C4.2, C5.2, C6.2, C7.2, C8.2, C9.1, C12.2, H1.1, H2.1, H3.1, H4.1, J1.5 (GND), J1.7 (GND), J1.11 (GNDDetect), J2.3, J3.2, R2.2, R4.2, R6.2, R7.2, R10.2, R11.2, SW2.C, U1.14 (VSSA), U1.16 (VSS), U1.32 (VSS), U2.4 (V-), U3.4 (V-), U3.5 (+), U3.6 (-), U5.1 (GND)
GPIO1: U1.5 (PA0), U2.1
GPIO2: U1.6 (PA1), U2.7
GPIO3: U1.9 (PA4), U3.1
NRST: C2.1, J1.12 (~RST), U1.4 (PG10)
unnamed: Flex1pos1.1, R3.2, R4.1, U2.3 (+)
unnamed: Flex1neg1.1, R1.1, R2.1, U2.2 (-)
unnamed: Flex2pos1.1, R5.2, R6.1, U2.5 (+)
unnamed: Flex2neg1.1, R7.1, R8.1, U2.6 (-)
unnamed: Flex3pos1.1, R9.2, R10.1, U3.3 (+)
unnamed: Flex3neg1.1, R11.1, R12.1, U3.2 (-)
SWCLK: J1.6 (JCLK/SWCLK), U1.24 (PA14)
SWDIO: J1.4 (JTMS/SWDIO), U1.23 (PA13)
UART1_HC05_RX: J2.5, U1.20 (PA10)
UART1_HC05_TX: J2.4, U1.19 (PA9)
UART2_DEBUG_RX: J1.13 (VCP_RX), U1.8 (PA3)
UART2_DEBUG_TX: J1.14 (VCP_TX), U1.7 (PA2)

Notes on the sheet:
Volume
1:key 6:state
Trous de fixation
±30%
HCO5/bluetooth
Flex1
Microprocesseur STM32G431KBT6
Sonde Debug
Flex2
Buck
batterie
Flex3

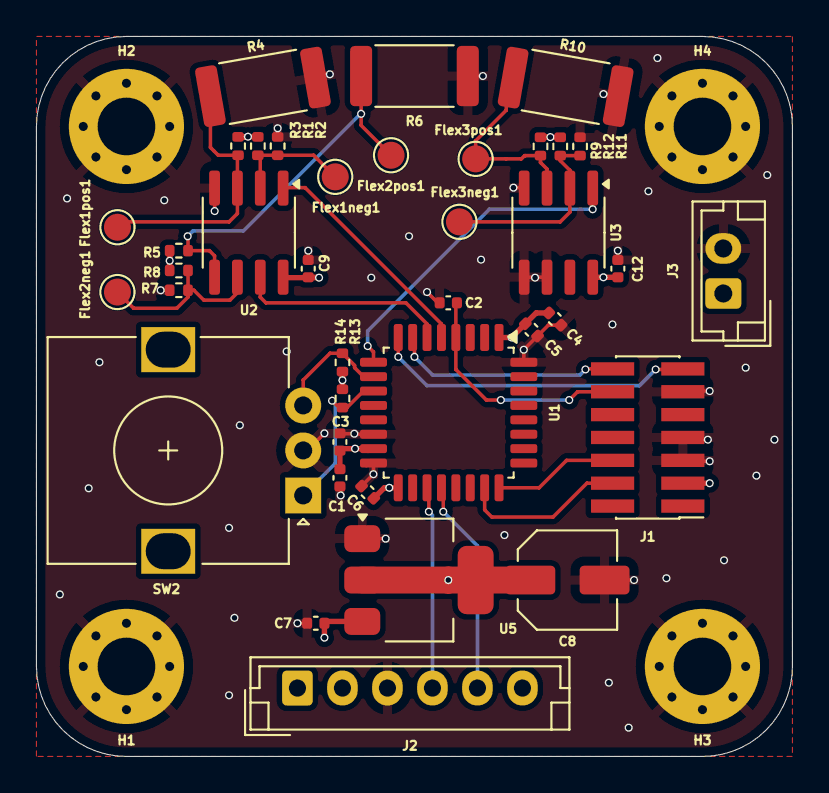
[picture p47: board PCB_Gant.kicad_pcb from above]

Board: 4 copper layers, 42.0 x 40.0 mm, 42 parts (0 on the bottom side), 21 nets.

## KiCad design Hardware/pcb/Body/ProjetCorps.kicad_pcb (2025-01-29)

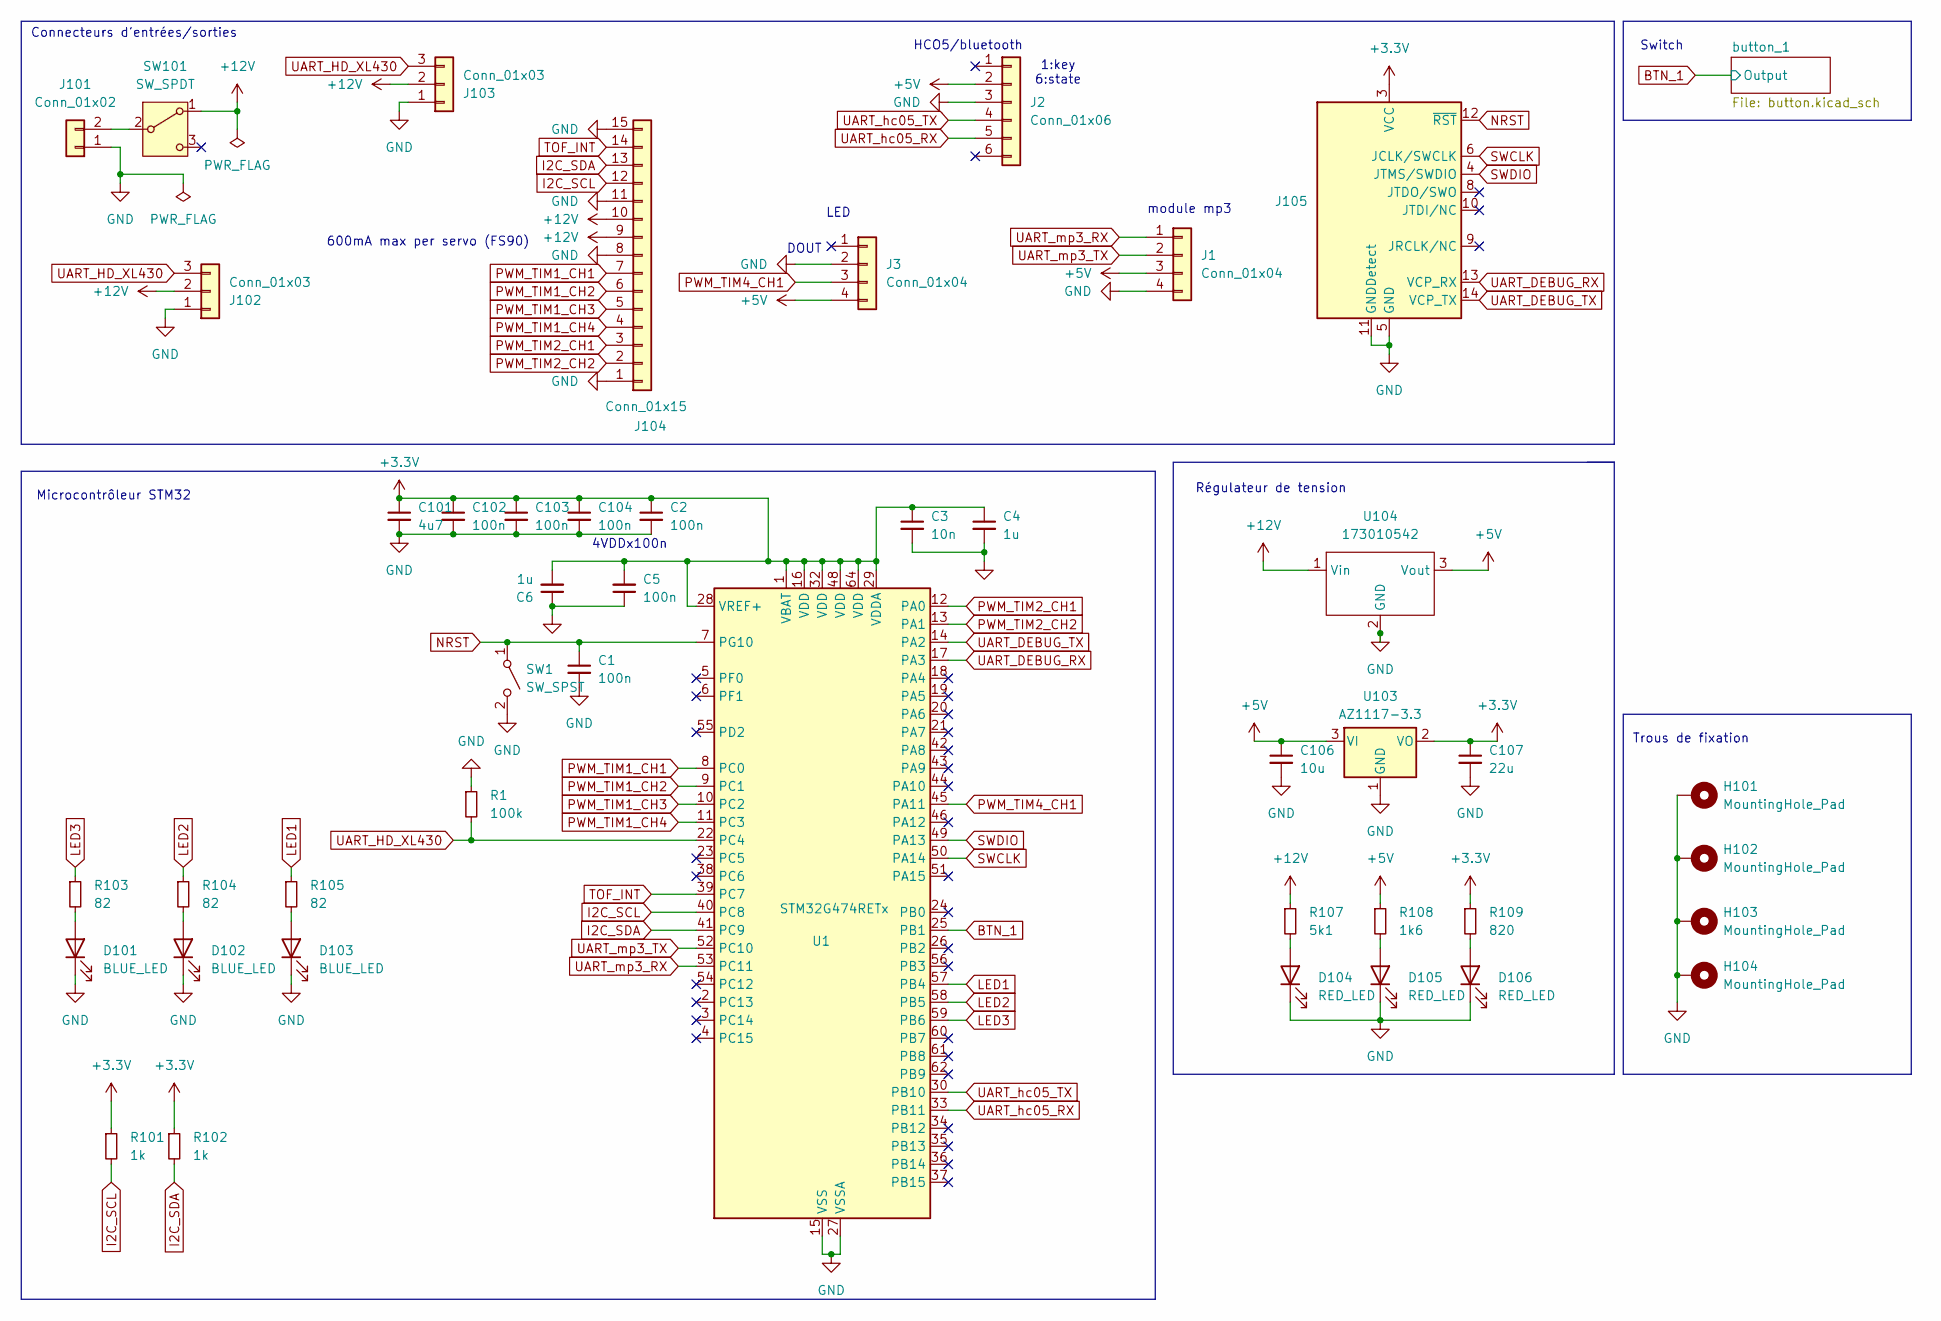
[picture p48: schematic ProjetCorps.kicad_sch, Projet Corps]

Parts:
C1, C2, C5, C102, C103, C104: 100n; C_0402_1005Metric
C3: 10n; C_0402_1005Metric
C4, C6: 1u; C_0402_1005Metric
C101: 4u7; C_0402_1005Metric
C106: 10u; C_0402_1005Metric
C107: 22u; C_Elec_5x5.4
D101, D102, D103: BLUE_LED; LED_0603_1608Metric; MPN 150060BS55040
D104, D105, D106: RED_LED; LED_0603_1608Metric; MPN 150060RS55040
H101, H102, H103, H104: MountingHole_Pad; MountingHole_3.2mm_M3_Pad_Via
J1, J3: Conn_01x04; JST_EH_B4B-EH-A_1x04_P2.50mm_Vertical
J2: Conn_01x06; JST_EH_B6B-EH-A_1x06_P2.50mm_Vertical
J101: Conn_01x02; AMASS_XT60-M_1x02_P7.20mm_Vertical
J102, J103: Conn_01x03; JST_EH_B3B-EH-A_1x03_P2.50mm_Vertical
J104: Conn_01x15; CONN15_31321_WRE; MPN 618015231421
J105: Conn_ST_STDC14; PinHeader_2x07_P1.27mm_Vertical_SMD
R1: 100k; R_0805_2012Metric
R101, R102: 1k; R_0402_1005Metric
R103, R104, R105: 82; R_0402_1005Metric
R107: 5k1; R_0402_1005Metric
R108: 1k6; R_0402_1005Metric
R109: 820; R_0402_1005Metric
SW1: SW_SPST; SW_Push_1P1T_NO_6x6mm_H9.5mm
SW101: SW_SPDT; 472123010111; MPN 472123010111
U1: STM32G474RETx; LQFP-64_10x10mm_P0.5mm
U103: AZ1117-3.3; SOT-223-3_TabPin2; MPN AZ1117CH2-3.3TRG1
U104: 173010542

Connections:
+3.3V: C2.1, C3.1, C4.1, C5.2, C6.2, C101.1, C102.1, C103.1, C104.1, C107.1, J105.3 (VCC), R101.1, R102.1, R109.1, U1.1 (VBAT), U1.16 (VDD), U1.28 (VREF+), U1.29 (VDDA), U1.32 (VDD), U1.48 (VDD), U1.64 (VDD), U103.2 (VO); also elsewhere on the board
+5V: C106.1, J1.3, J2.2, J3.4, R108.1, U103.3 (VI), U104.3 (Vout)
+12V: J102.2, J103.2, J104.9, J104.10, R107.1, SW101.1 (A), U104.1 (Vin)
BTN_1: U1.25 (PB1); also elsewhere on the board
GND: C1.2, C2.2, C3.2, C4.2, C5.1, C6.1, C101.2, C102.2, C103.2, C104.2, C106.2, C107.2, D101.1 (K), D102.1 (K), D103.1 (K), D104.1 (K), D105.1 (K), D106.1 (K), H101.1, H102.1, H103.1, H104.1, J1.4, J2.3, J3.2, J101.1, J102.1, J103.1, J104.1, J104.8, J104.11, J104.15, J105.5 (GND), J105.7 (GND), J105.11 (GNDDetect), R1.1, SW1.2 (B), U1.15 (VSS), U1.27 (VSSA), U1.31 (VSS), U1.47 (VSS), U1.63 (VSS), U103.1 (GND), U104.2 (GND); also elsewhere on the board
I2C_SCL: J104.12, R101.2, U1.40 (PC8)
I2C_SDA: J104.13, R102.2, U1.41 (PC9)
LED1: R105.1, U1.57 (PB4)
LED2: R104.1, U1.58 (PB5)
LED3: R103.1, U1.59 (PB6)
NRST: C1.1, J105.12 (~RST), SW1.1 (A), U1.7 (PG10)
unnamed: D101.2 (A), R103.2
unnamed: D102.2 (A), R104.2
unnamed: D103.2 (A), R105.2
unnamed: D104.2 (A), R107.2
unnamed: D105.2 (A), R108.2
unnamed: D106.2 (A), R109.2
unnamed: J101.2, SW101.2 (B)
PWM_TIM1_CH1: J104.7, U1.8 (PC0)
PWM_TIM1_CH2: J104.6, U1.9 (PC1)
PWM_TIM1_CH3: J104.5, U1.10 (PC2)
PWM_TIM1_CH4: J104.4, U1.11 (PC3)
PWM_TIM2_CH1: J104.3, U1.12 (PA0)
PWM_TIM2_CH2: J104.2, U1.13 (PA1)
PWM_TIM4_CH1: J3.3, U1.45 (PA11)
SWCLK: J105.6 (JCLK/SWCLK), U1.50 (PA14)
SWDIO: J105.4 (JTMS/SWDIO), U1.49 (PA13)
TOF_INT: J104.14, U1.39 (PC7)
UART_DEBUG_RX: J105.13 (VCP_RX), U1.17 (PA3)
UART_DEBUG_TX: J105.14 (VCP_TX), U1.14 (PA2)
UART_HD_XL430: J102.3, J103.3, R1.2, U1.22 (PC4)
UART_hc05_RX: J2.5, U1.33 (PB11)
UART_hc05_TX: J2.4, U1.30 (PB10)
UART_mp3_RX: J1.1, U1.53 (PC11)
UART_mp3_TX: J1.2, U1.52 (PC10)

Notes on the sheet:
HCO5/bluetooth
600mA max per servo (FS90)
module mp3
Microcontrôleur STM32
Switch
Connecteurs d'entrées/sorties
Trous de fixation
1:key 6:state
LED
4VDDx100n
Régulateur de tension
DOUT

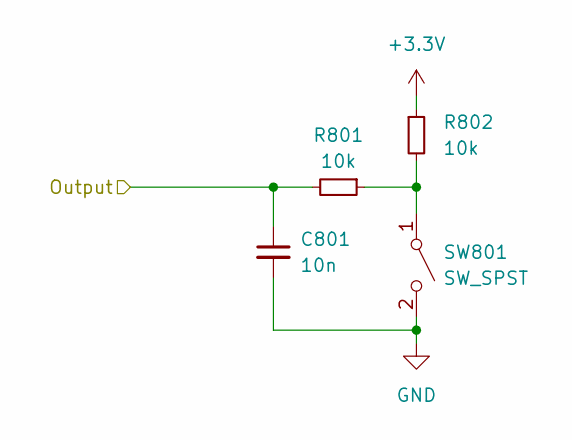
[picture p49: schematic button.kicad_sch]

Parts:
C801: 10n; C_0402_1005Metric
R801, R802: 10k; R_0402_1005Metric
SW801: SW_SPST; SW_Push_1P1T_NO_6x6mm_H9.5mm

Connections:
+3.3V: R802.1; also elsewhere on the board
BTN_1: C801.1, R801.2; also elsewhere on the board
GND: C801.2, SW801.2 (B); also elsewhere on the board
unnamed: R801.1, R802.2, SW801.1 (A)

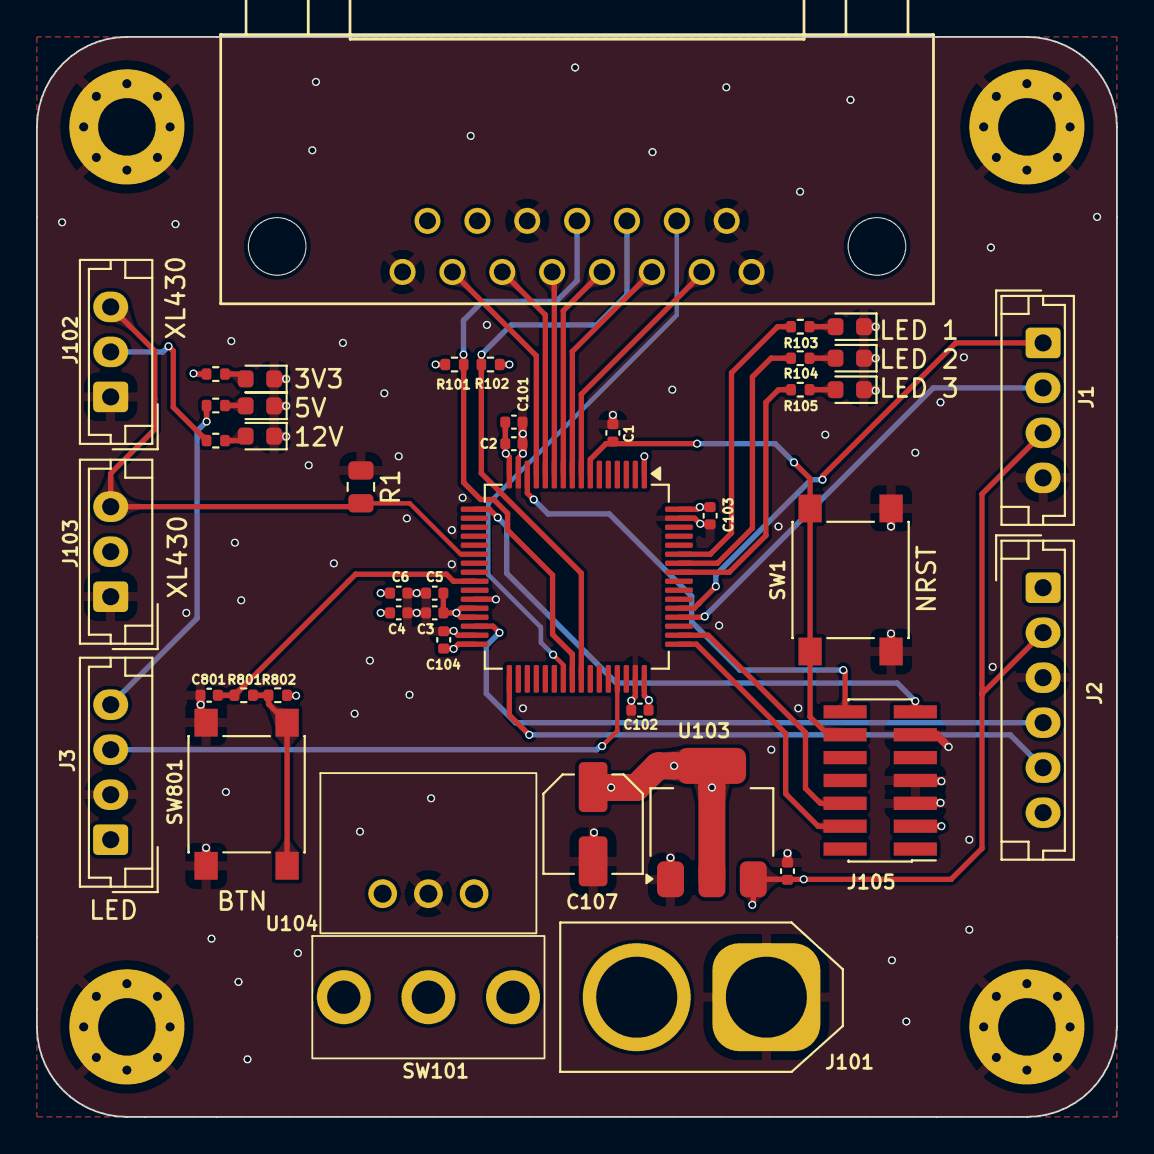
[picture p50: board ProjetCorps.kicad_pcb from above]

Board: 4 copper layers, 60.0 x 60.0 mm, 48 parts (0 on the bottom side), 36 nets.

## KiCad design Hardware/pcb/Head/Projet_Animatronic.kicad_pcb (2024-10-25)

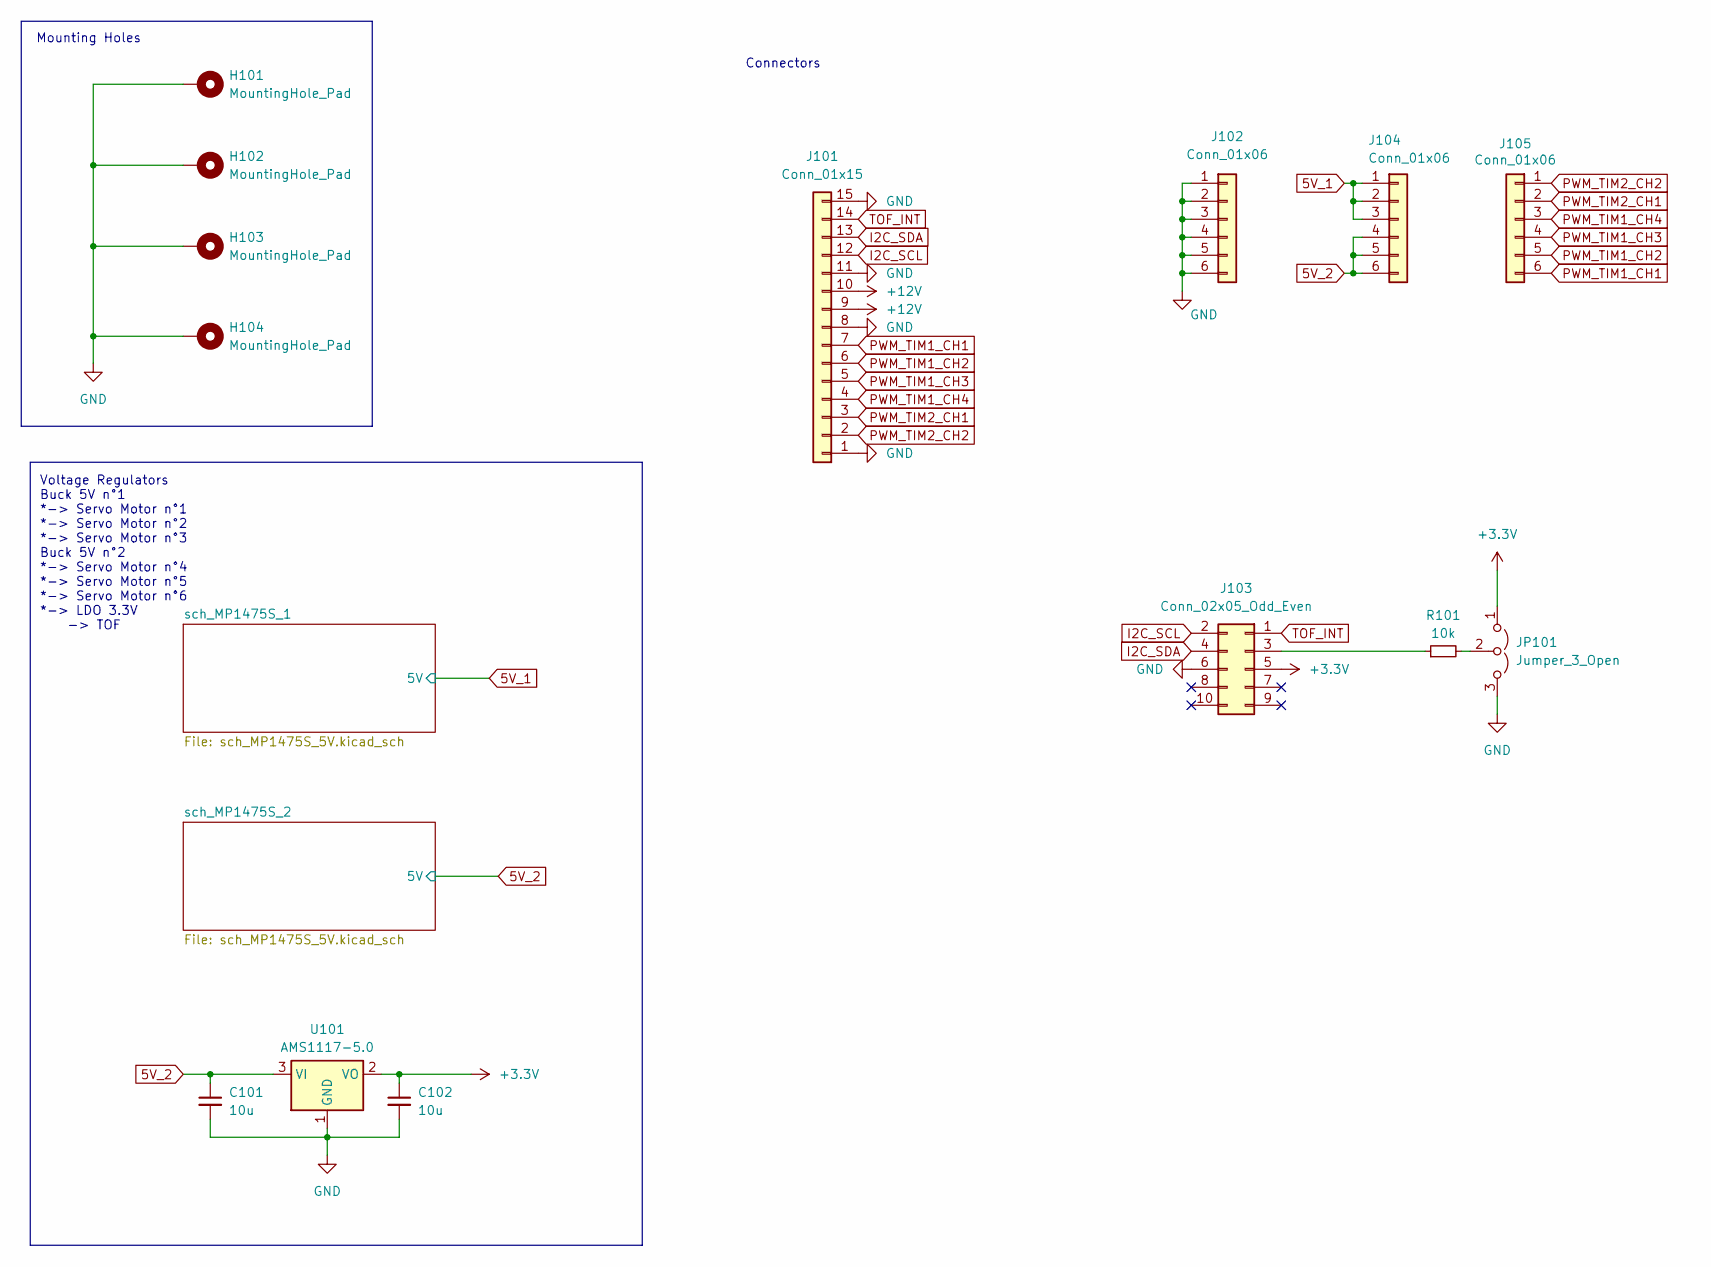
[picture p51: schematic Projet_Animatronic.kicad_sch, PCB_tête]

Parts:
C101, C102: 10u; C_0603_1608Metric
H101, H102, H103, H104: MountingHole_Pad; MountingHole_3.2mm_M3_Pad_Via
J101: Conn_01x15; CONN15_31321_WRE; MPN 618015231321
J102, J104, J105: Conn_01x06; PinHeader_1x06_P2.54mm_Vertical
J103: Conn_02x05_Odd_Even; PinHeader_2x05_P2.54mm_Vertical
JP101: Jumper_3_Open; SolderJumper-3_P1.3mm_Open_RoundedPad1.0x1.5mm_NumberLabels
R101: 10k; R_0603_1608Metric
U101: AMS1117-5.0; SOT-223-3_TabPin2

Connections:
5V_1: J104.1, J104.2, J104.3; also elsewhere on the board
5V_2: C101.1, J104.4, J104.5, J104.6, U101.3 (VI); also elsewhere on the board
+3.3V: C102.1, J103.5, JP101.1 (A), U101.2 (VO)
+12V: J101.9, J101.10; also elsewhere on the board
GND: C101.2, C102.2, H101.1, H102.1, H103.1, H104.1, J101.1, J101.8, J101.11, J101.15, J102.1, J102.2, J102.3, J102.4, J102.5, J102.6, J103.6, JP101.3 (B), U101.1 (GND); also elsewhere on the board
I2C_SCL: J101.12, J103.2
I2C_SDA: J101.13, J103.4
unnamed: J103.3, R101.1
unnamed: JP101.2 (C), R101.2
PWM_TIM1_CH1: J101.7, J105.6
PWM_TIM1_CH2: J101.6, J105.5
PWM_TIM1_CH3: J101.5, J105.4
PWM_TIM1_CH4: J101.4, J105.3
PWM_TIM2_CH1: J101.3, J105.2
PWM_TIM2_CH2: J101.2, J105.1
TOF_INT: J101.14, J103.1

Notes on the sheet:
Voltage Regulators Buck 5V n°1 *-> Servo Motor n°1 *-> Servo Motor n°2 *-> Servo Motor n°3 Buck 5V n°2 *-> Servo Motor n°4 *-> Servo Motor n°5 *-> Servo Motor n°6 *-> LDO 3.3V -> TOF
Connectors
Mounting Holes

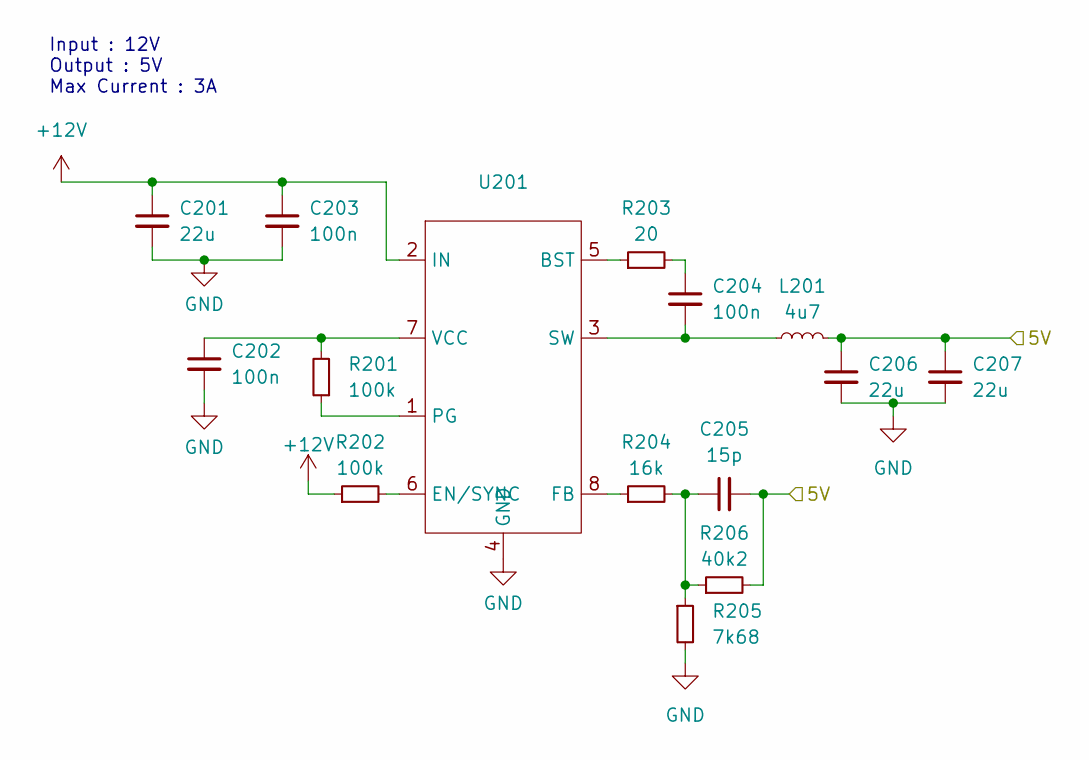
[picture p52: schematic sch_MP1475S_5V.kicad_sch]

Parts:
C201, C207: 22u; C_0805_2012Metric
C202, C203, C204: 100n; C_0603_1608Metric
C205: 15p; C_0603_1608Metric
C206: 22u; C_0603_1608Metric
L201: 4u7; 74404052047; MPN 74404052047
R201, R202: 100k; R_0603_1608Metric
R203: 20; R_0603_1608Metric
R204: 16k; R_0603_1608Metric
R205: 7k68; R_0603_1608Metric
R206: 40k2; R_0603_1608Metric
U201: TSOT-23-8

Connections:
5V_1: C205.2, C206.1, C207.1, L201.2, R206.2; also elsewhere on the board
+12V: C201.1, C203.1, R202.1, U201.2 (IN); also elsewhere on the board
GND: C201.2, C202.2, C203.2, C206.2, C207.2, R205.2, U201.4 (GND); also elsewhere on the board
unnamed: C204.1, R203.2
unnamed: C205.1, R204.2, R205.1, R206.1
unnamed: R203.1, U201.5 (BST)
unnamed: R202.2, U201.6 (EN/SYNC)
unnamed: R204.1, U201.8 (FB)
unnamed: R201.1, U201.1 (PG)
unnamed: C204.2, L201.1, U201.3 (SW)
unnamed: C202.1, R201.2, U201.7 (VCC)

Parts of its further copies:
C301, C307: 22u; C_0805_2012Metric
C302, C303, C304: 100n; C_0603_1608Metric
C305: 15p; C_0603_1608Metric
C306: 22u; C_0603_1608Metric
L301: 4u7; 74404052047; MPN 74404052047
R301, R302: 100k; R_0603_1608Metric
R303: 20; R_0603_1608Metric
R304: 16k; R_0603_1608Metric
R305: 7k68; R_0603_1608Metric
R306: 40k2; R_0603_1608Metric
U301: TSOT-23-8

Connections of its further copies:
5V_2: C305.2, C306.1, C307.1, L301.2, R306.2; also elsewhere on the board
+12V: C301.1, C303.1, R302.1, U301.2 (IN); also elsewhere on the board
GND: C301.2, C302.2, C303.2, C306.2, C307.2, R305.2, U301.4 (GND); also elsewhere on the board
unnamed: C304.1, R303.2
unnamed: C305.1, R304.2, R305.1, R306.1
unnamed: R303.1, U301.5 (BST)
unnamed: R302.2, U301.6 (EN/SYNC)
unnamed: R304.1, U301.8 (FB)
unnamed: R301.1, U301.1 (PG)
unnamed: C304.2, L301.1, U301.3 (SW)
unnamed: C302.1, R301.2, U301.7 (VCC)

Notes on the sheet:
Input : 12V Output : 5V Max Current : 3A

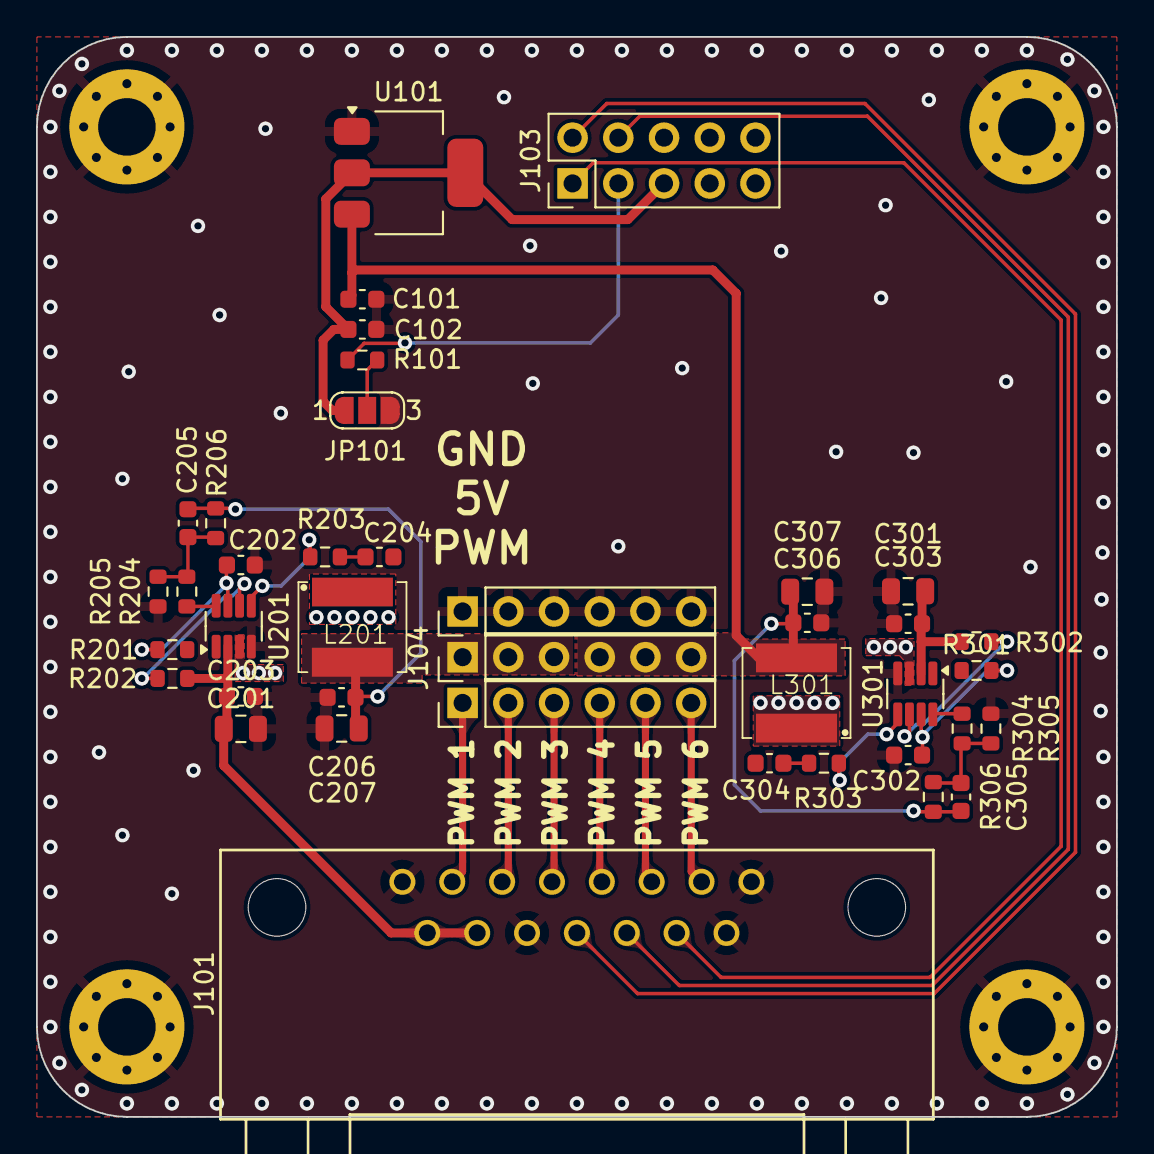
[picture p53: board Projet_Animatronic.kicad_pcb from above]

Board: 2 copper layers, 60.0 x 60.0 mm, 44 parts (0 on the bottom side), 32 nets.

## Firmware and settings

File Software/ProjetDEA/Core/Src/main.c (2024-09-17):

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
/* Includes ------------------------------------------------------------------*/
#include "main.h"
#include <stdio.h>
#include <stm32l4xx_hal.h>
#include "servo.h"

I2C_HandleTypeDef hi2c3;

TIM_HandleTypeDef htim1;
TIM_HandleTypeDef htim2;

UART_HandleTypeDef huart1;
UART_HandleTypeDef huart2;

void SystemClock_Config(void);
static void MX_GPIO_Init(void);
static void MX_TIM1_Init(void);
static void MX_USART1_UART_Init(void);
static void MX_USART2_UART_Init(void);
static void MX_I2C3_Init(void);
static void MX_TIM2_Init(void);
/* USER CODE BEGIN 0 */
#ifdef __GNUC__
#define PUTCHAR_PROTOTYPE int __io_putchar(int ch)
#define GETCHAR_PROTOTYPE int __io_getchar(void)
#else
#define PUTCHAR_PROTOTYPE int fputc(int ch, FILE *f)
#define GETCHAR_PROTOTYPE int fgetc(FILE *f)
#endif

PUTCHAR_PROTOTYPE
{
  HAL_UART_Transmit(&huart2, (uint8_t *)&ch, 1, HAL_MAX_DELAY);
  return ch;
}


GETCHAR_PROTOTYPE
{
  uint8_t ch = 0;

  /* Clear the Overrun flag just before receiving the first character */
  __HAL_UART_CLEAR_OREFLAG(&huart2);

  /* Wait for reception of a character on the USART RX line and echo this
   * character on console */
  HAL_UART_Receive(&huart2, (uint8_t *)&ch, 1, HAL_MAX_DELAY);
  HAL_UART_Transmit(&huart2, (uint8_t *)&ch, 1, HAL_MAX_DELAY);
  return ch;
}
/* USER CODE END 0 */

/**
  * @brief  The application entry point.
  * @retval int
  */
int main(void)
{
  /* MCU Configuration--------------------------------------------------------*/

  /* Reset of all peripherals, Initializes the Flash interface and the Systick. */
  HAL_Init();

  /* Configure the system clock */
  SystemClock_Config();

  /* Initialize all configured peripherals */
  MX_GPIO_Init();
  MX_TIM1_Init();
  MX_USART1_UART_Init();
  MX_USART2_UART_Init();
  MX_I2C3_Init();
  MX_TIM2_Init();
  /* USER CODE BEGIN 2 */

  HAL_TIM_PWM_Start(&htim1, TIM_CHANNEL_1);
  HAL_TIM_PWM_Start(&htim1, TIM_CHANNEL_2);
  HAL_TIM_PWM_Start(&htim1, TIM_CHANNEL_3);
  HAL_TIM_PWM_Start(&htim1, TIM_CHANNEL_4);
  HAL_TIM_PWM_Start(&htim2, TIM_CHANNEL_1);
  HAL_TIM_PWM_Start(&htim2, TIM_CHANNEL_2);

  /*__XL430_HandleTypeDef XL430_1;

  XL430_Init(&XL430_1, &huart2, 1, 1);
  XL430_Init_debug(&XL430_1, &huart2, &huart1, 1, 1);
  XL430_Ping(&XL430_1);
  XL430_Write_Data(&XL430_1,XL430_REG_TORQUE_ENABLE,0);
  XL430_Set_Operating_Mode(&XL430_1,XL430_VELOCITY_CONTROL_MODE);
  XL430_Set_Speed(&XL430_1,200);
  XL430_Write_Data(&XL430_1,XL430_REG_TORQUE_ENABLE,1);*/

  __Servo_HandleTypeDef Servo_1;
  __Servo_HandleTypeDef Servo_2;
  __Servo_HandleTypeDef Servo_3;

  /* USER CODE END 2 */

  servoInit(&Servo_1, GPIOB, BTN_1_Pin, &htim1, TIM_CHANNEL_4);
  servoInit(&Servo_2, GPIOB, BTN_2_Pin, &htim1, TIM_CHANNEL_3);
  servoInit(&Servo_3, GPIOA, BTN_3_Pin, &htim1, TIM_CHANNEL_2);

  /* Infinite loop */
  /* USER CODE BEGIN WHILE */
  while (1)
  {
	  if(btnPressed() != 0){
		  int a = btnPressed();
		  switch(a){
		  	  case 1:
		  		  turnServo(&Servo_1);
		  		  break;
		  	  case 2:
		  		  turnServo(&Servo_2);
		  		  break;
		  	  case 3:
		  		  turnServo(&Servo_3);
		  		  break;
		  	  default:
		  }
	  }


    /* USER CODE END WHILE */

    /* USER CODE BEGIN 3 */
  }
  /* USER CODE END 3 */
}

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


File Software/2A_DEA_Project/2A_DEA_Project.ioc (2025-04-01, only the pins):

Mcu.UserName=STM32G474RETx
PA0.GPIO_Label=PWM 2
PA0.Signal=S_TIM2_CH1
PA1.GPIO_Label=PWM 1
PA1.Signal=S_TIM2_CH2
PA11.Signal=S_TIM4_CH1
PA13.Signal=SYS_JTMS-SWDIO
PA14.Signal=SYS_JTCK-SWCLK
PA2.GPIO_Label=USART2_TX (sonde)
PA2.Signal=USART2_TX
PA3.GPIO_Label=USART2_RX (sonde)
PA3.Signal=USART2_RX
PA9.Signal=S_TIM2_CH3
PB1.GPIO_Label=BTN_1
PB1.Signal=GPIO_Input
PB10.GPIO_Label=USART3_TX (hc05)
PB10.Signal=USART3_TX
PB11.GPIO_Label=USART3_RX (hc05)
PB11.Signal=USART3_RX
PB4.GPIO_Label=LED1
PB4.Signal=GPIO_Output
PB5.GPIO_Label=LED2
PB5.Signal=GPIO_Output
PB6.GPIO_Label=LED3
PB6.Signal=GPIO_Output
PC0.GPIO_Label=PWM 6
PC0.Signal=S_TIM1_CH1
PC1.GPIO_Label=PWM 5
PC1.Signal=S_TIM1_CH2
PC10.GPIO_Label=UART4_TX (mp3)
PC10.Signal=UART4_TX
PC11.GPIO_Label=UART4_RX (mp3)
PC11.Signal=UART4_RX
PC2.GPIO_Label=PWM 4
PC2.Signal=S_TIM1_CH3
PC3.GPIO_Label=PWM 3
PC3.Signal=S_TIM1_CH4
PC4.GPIO_Label=USART1_TX (xl430)
PC4.Signal=USART1_TX
PC7.GPIO_Label=TOF_GPIO
PC7.Signal=GPIO_Input
PC8.Signal=I2C3_SCL
PC9.Signal=I2C3_SDA

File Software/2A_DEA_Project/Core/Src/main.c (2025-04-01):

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
/* Includes ------------------------------------------------------------------*/
#include "main.h"
#include "dma.h"
#include "i2c.h"
#include "tim.h"
#include "usart.h"
#include "gpio.h"

/* USER CODE BEGIN Includes */
#include <stdio.h>
#include "stm32g4xx_hal.h"
#include "xl430.h"
#include "neopixel.h"
#include "mp3.h"
#include "bluetooth_protocol.h"
#include "VL53L1X_api.h"
#include "vl53l1_error_codes.h"

/* USER CODE END Includes */

/* USER CODE BEGIN PD */
#define VL53L1X_DEFAULT_ADDRESS (0x29 << 1)

#ifdef __GNUC__
#define PUTCHAR_PROTOTYPE int __io_putchar(int ch)
#else
#define PUTCHAR_PROTOTYPE int fputc(int ch, FILE *f)
#endif
/* USER CODE END PD */


void SystemClock_Config(void);
/* USER CODE BEGIN 0 */
#ifdef __GNUC__
#define PUTCHAR_PROTOTYPE int __io_putchar(int ch)
#define GETCHAR_PROTOTYPE int __io_getchar(void)
#else
#define PUTCHAR_PROTOTYPE int fputc(int ch, FILE *f)
#define GETCHAR_PROTOTYPE int fgetc(FILE *f)
#endif

PUTCHAR_PROTOTYPE {
    HAL_UART_Transmit(&huart2, (uint8_t *)&ch, 1, HAL_MAX_DELAY);
    return ch;
}

GETCHAR_PROTOTYPE
{
	uint8_t ch = 0;

	/* Clear the Overrun flag just before receiving the first character */
	__HAL_UART_CLEAR_OREFLAG(&huart2);

	/* Wait for reception of a character on the USART RX line and echo this
	 * character on console */
	HAL_UART_Receive(&huart2, (uint8_t *)&ch, 1, HAL_MAX_DELAY);
	HAL_UART_Transmit(&huart2, (uint8_t *)&ch, 1, HAL_MAX_DELAY);
	return ch;
}

///////////////////////////////////////////////// TOF ////////////////////////////////////////////////////////////////////

//uint32_t measure_counter = 0;
//uint8_t data_available = 0;
//
//void HAL_GPIO_EXTI_Callback(uint16_t GPIO_Pin)
//{
//	if (TOF_GPIO_Pin == GPIO_Pin)
//	{
//		measure_counter++;
//		data_available++;
//	}
//}

//////////////////////////////////////////// Bluetooth protocol //////////////////////////////////////////////////////////

//char startChar = '@';
//char endChar = '#';
//
//uint8_t rx_char; // Variable to store the received character
//
//char instruction[200];
//int instructionIndex = 0;
//
//int UARTReceiverState = 0;
//
//volatile int flagUART1 = 0;
//
//
//void HAL_UART_RxCpltCallback(UART_HandleTypeDef *huart) {
//	// Re-enable UART interrupt reception
//	HAL_UART_Receive_IT(&huart3, &rx_char, 1);
//
//	instruction[instructionIndex] = rx_char;
//	instructionIndex++;
//
//	if (rx_char == '#')
//	{
//		instruction[instructionIndex] = 0; // 0 character for the printf
//		instructionIndex = 0;
//		flagUART1 = 1;
//	}
//}

/* USER CODE END 0 */

/**
  * @brief  The application entry point.
  * @retval int
  */
int main(void)
{

  /* MCU Configuration--------------------------------------------------------*/

  /* Reset of all peripherals, Initializes the Flash interface and the Systick. */
  HAL_Init();

  /* Configure the system clock */
  SystemClock_Config();

  /* Initialize all configured peripherals */
  MX_GPIO_Init();
  MX_DMA_Init();
  MX_TIM1_Init();
  MX_TIM2_Init();
  MX_UART4_Init();
  MX_USART1_UART_Init();
  MX_USART2_UART_Init();
  MX_USART3_UART_Init();
  MX_I2C3_Init();
  MX_TIM4_Init();
  /* USER CODE BEGIN 2 */


  /////////////////////////////////////////////// Tests XL430 ////////////////////////////////////////////////////////////////

	printf("\r\n===== ANIMATRONIC EAGLE FUCK YEAH =====\r\n");
	__XL430_HandleTypeDef XL430_1;
//	__XL430_HandleTypeDef XL430_2;
//	__XL430_HandleTypeDef XL430_3;
//	__XL430_HandleTypeDef XL430_4;
//	__XL430_HandleTypeDef XL430_5;
//	__XL430_HandleTypeDef XL430_6;
//
	XL430_Init(&XL430_1, &huart1, 1, 0);
	XL430_Init_debug(&XL430_1, &huart1, &huart2, 1, 0);
	HAL_Delay(300);
	XL430_Write_Data2(&XL430_1,XL430_REG_TORQUE_ENABLE,1);
	(&XL430_1)->torque_enable = 1;
//
//	XL430_Init(&XL430_2, &huart1, 2, 0);
//	XL430_Init_debug(&XL430_2, &huart1, &huart2, 2, 0);
//	HAL_Delay(200);
//	XL430_Write_Data2(&XL430_2,XL430_REG_TORQUE_ENABLE,1);
//	(&XL430_2)->torque_enable = 1;
//
//	XL430_Init(&XL430_3, &huart1, 3, 0);
//	XL430_Init_debug(&XL430_3, &huart1, &huart2, 3, 0);
//	HAL_Delay(200);
//	XL430_Write_Data2(&XL430_3,XL430_REG_TORQUE_ENABLE,1);
//	(&XL430_3)->torque_enable = 1;
//	HAL_Delay(200);
//
//	XL430_Init(&XL430_4, &huart1, 4, 0);
//	XL430_Init_debug(&XL430_4, &huart1, &huart2, 4, 0);
//	HAL_Delay(300);
//	XL430_Write_Data2(&XL430_4,XL430_REG_TORQUE_ENABLE,1);
//	(&XL430_4)->torque_enable = 1;
//	HAL_Delay(300);
//
//	XL430_Init(&XL430_5, &huart1, 5, 0);
//	XL430_Init_debug(&XL430_5, &huart1, &huart2, 5, 0);
//	HAL_Delay(300);
//	XL430_Write_Data2(&XL430_5,XL430_REG_TORQUE_ENABLE,1);
//	(&XL430_5)->torque_enable = 1;
//	HAL_Delay(300);
//
//	XL430_Init(&XL430_6, &huart1, 6, 0);
//	XL430_Init_debug(&XL430_6, &huart1, &huart2, 6, 0);
//	HAL_Delay(300);
//	XL430_Write_Data2(&XL430_6,XL430_REG_TORQUE_ENABLE,1);
//	(&XL430_6)->torque_enable = 1;
//	HAL_Delay(300);
//
//	XL430_Write_Data2(&XL430_4,XL430_REG_GOAL_VELOCITY,40);
//	HAL_Delay(1000);
//	XL430_Write_Data2(&XL430_4,XL430_REG_GOAL_VELOCITY,0);
//	HAL_Delay(300);
//	XL430_Write_Data2(&XL430_5,XL430_REG_GOAL_VELOCITY,-40);
//	HAL_Delay(1000);
//	XL430_Write_Data2(&XL430_5,XL430_REG_GOAL_VELOCITY,40);
//	HAL_Delay(1000);
//	XL430_Write_Data2(&XL430_5,XL430_REG_GOAL_VELOCITY,0);
//	HAL_Delay(300);
//	XL430_Write_Data2(&XL430_4,XL430_REG_GOAL_VELOCITY,-40);
//	HAL_Delay(1000);
//	XL430_Write_Data2(&XL430_4,XL430_REG_GOAL_VELOCITY,0);
//

	XL430_Write_Data2(&XL430_1,XL430_REG_GOAL_VELOCITY,-40);
	printf("jaaj\n\r");
	HAL_Delay(2000);
	XL430_Write_Data2(&XL430_1,XL430_REG_GOAL_VELOCITY,40);
	printf("jaaj\n\r");
	HAL_Delay(2000);
	XL430_Write_Data2(&XL430_1,XL430_REG_GOAL_VELOCITY,0);
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

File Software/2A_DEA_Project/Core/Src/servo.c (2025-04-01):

/*
 * servo.c
 *
 *  Created on: Mar 11, 2025
 *      Author: administrateur
 */

#include "servo.h"

void servoInit(h_servo_t *servoHandle, TIM_HandleTypeDef *timer, uint32_t timerChannel) {
	servoHandle->timer = timer;
	servoHandle->timerChannel = timerChannel;
	servoHandle->pos0 = 250;
	servoHandle->pos1 = 1250;
	HAL_TIM_PWM_Start(servoHandle->timer, servoHandle->timerChannel);
	__HAL_TIM_SET_COMPARE(servoHandle->timer, servoHandle->timerChannel, servoHandle->pos0);
	servoHandle->currentPos = 0;
}

void turnServo(h_servo_t *servoHandle) {
	if (servoHandle->currentPos == 0) {
		__HAL_TIM_SET_COMPARE(servoHandle->timer, servoHandle->timerChannel, servoHandle->pos1);
	}
	if (servoHandle->currentPos == 1) {
		__HAL_TIM_SET_COMPARE(servoHandle->timer, servoHandle->timerChannel, servoHandle->pos0);
	}
	servoHandle->currentPos = 1 - servoHandle->currentPos;
}

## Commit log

2024-09-17 Imports de l'année dernière
2024-10-01 nouveaux PCBs
    [ProjetCorps-B_Cu.gbr, ProjetCorps-B_Mask.gbr, ProjetCorps-B_Paste.gbr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]
2024-10-08 led ds
2024-10-15 maj PCB
    [ProjetCorps.kicad_pcb, ProjetCorps.kicad_sch, Projet_Animatronic.kicad_sch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]
2024-10-22 update pcb body
    [ProjetCorps.kicad_pcb, ProjetCorps.kicad_sch]
2024-10-22 check Fiack
    [ProjetCorps.kicad_pcb, ProjetCorps.kicad_sch, button.kicad_sch]
2024-10-22 update tof int
    [ProjetCorps.kicad_pcb, ProjetCorps.kicad_sch]
2024-10-22 gerber pcb body
    [ProjetCorps-B_Cu.gbr, ProjetCorps-B_Mask.gbr, ProjetCorps-B_Paste.gbr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]
2024-10-25 gerber pcb head
    [Projet_Animatronic-B_Cu.gbr, Projet_Animatronic-B_Mask.gbr, Projet_Animatronic-B_Paste.gbr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]
2025-01-14 organized hardware
    [Part Studio 1 - Part 1.step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]
2025-01-14 fichiers stl
    [Humérus.stl, Liaisonhumérus-radius1.stl, Liaisonhumérus-radius2.stl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]
2025-01-21 added mp3 module driving via uart
2025-01-24 pcb gant
    [PCB_Gant.kicad_pcb, PCB_Gant.kicad_sch]
2025-01-24 modifications on schematic
    [PCB_Gant.kicad_sch]
2025-01-25 PCB gant v1
    [PCB_Gant.kicad_pcb, PCB_Gant.kicad_sch]
2025-01-28 PCB gant V2
    [PCB_Gant.kicad_pcb, PCB_Gant.kicad_sch]
2025-01-28 Datasheet rotary encoder
2025-01-28 pcb body & gant maj
    [PCB_Gant.kicad_pcb, PCB_Gant.kicad_sch, ProjetCorps.kicad_pcb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]
2025-01-28 PCB body & gant V3
    [PCB_Gant.kicad_pcb, PCB_Gant.kicad_sch, ProjetCorps.kicad_pcb]
2025-01-29 gerbers for body & gant
    [PCB_Gant-B_Cu.gbr, PCB_Gant-B_Mask.gbr, PCB_Gant-B_Paste.gbr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]
2025-04-01 screens PCB
    [PCB_Gant.csv, ProjetCorps.csv]
2025-04-01 rangement fichiers Stl
    [Humérus.stl, Liaisonhumérus-radius1.stl, Liaisonhumérus-radius2.stl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]
2025-04-01 update journal de bord
2025-04-01 add fichiers 3mf/stl
    [Tete aigle maillage reduit STEP - Part 3.3mf, Tete aigle maillage reduit STEP - Part 3.stl, Tete aigle maillage reduit STEP.3mf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]
2025-04-01 maj tableau bord test
    [Tete aigle maillage reduit STEP - paupière_left.stl, Tete aigle maillage reduit STEP - paupière_right.stl, Tete_aigle_full.stl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]

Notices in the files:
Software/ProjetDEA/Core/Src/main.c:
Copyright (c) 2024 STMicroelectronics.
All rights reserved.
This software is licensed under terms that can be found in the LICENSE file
